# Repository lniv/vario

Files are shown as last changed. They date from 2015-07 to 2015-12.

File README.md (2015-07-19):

# vario

A sailplane / soaring  variometer project.
Minimal use is as a standalone vario, using a pressure sensor (typically connected to a TE probe) to measure climb rate. The code running on a teensy 3.1  (using the teensyduino environment (but not the IDE (shudder)) drives an indicator gauge stepper and a speaker.
Optionally, a differential pressure sensor and a gps are connected to the uC, and information is sent to a flight computer.
Current protocol implemented is the open vario one, and the gps GPRMC sentences are just echoed.
Currently a 9dof imu is connected as well, but the data is not procssed. In the far future one could integrate barometric / imu / gps data to get a better state estimate.

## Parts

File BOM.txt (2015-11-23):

BOM

The following components were used - initially on a protoboard, moved onto a soldered setup. This is not the cheapest or smallest way to use the underlying components, but the point was to use a building block approach and avoid any surface mount soldering, or creating PCBs (though assembling all of these using 30 awg wire, as i've done, does resemble a rats nest - i will try to create a pcb for easily connecting all of these)

Adafruit 

1 x Teensy 3.1 + header[ID:1625] = $19.95
1 x Adafruit 10-DOF IMU Breakout - L3GD20H + LSM303 + BMP180[ID:1604] = $29.95
1 x Adafruit Mono 2.5W Class D Audio Amplifier - PAM8302[ID:2130] = $3.95
1 x Mini Metal Speaker w/ Wires - 8 ohm 0.5W[ID:1890] = $3.00
1 x Automotive Gauge Stepper Motor (x27.168) [ID:2424] = $9.95
1 x Adafruit TB6612 1.2A DC/Stepper Motor Driver Breakout Board[ID:2448] = $4.95

modern device -  Pressure Sensor (MPXV) (#MD0590) (honeywell MPXV7007DP) 14$
2 x 10K resistors (for MPXV7007DP voltage divider) - should be 1% or better.

Sparkfun:
1 x LS20031 gps module [Sparkfun GPS-08975] = 59.95$

1 x MS-5611 breakout module GY-63 [dealextreme #148866, numerous sources exist] = 14.35$

Notes:
currently the code does not use the gps (apart from forwarding it to the navigation computer), the diff pressure module (ditto - it does calculate airspeed, but does not use it for vario) and imu. Hence, a simpler BMP180 breakout board can be used and the gps and diff pressure modules can be dropped, or only the MS-5611 breakout module can be used (dropping gps, imu)

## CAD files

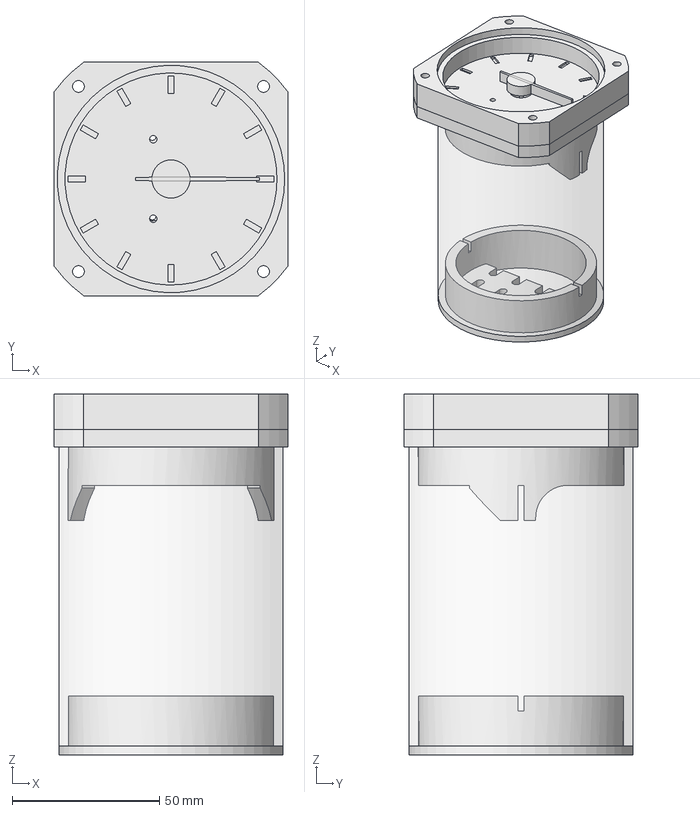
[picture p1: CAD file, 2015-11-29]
mechanical/v1/vario_assembly_v1.fcstd
79.4 x 79.4 x 122.6 mm
fron_window_holder_v1_01
vario_body_rev5_01
vario_rear_r2_01
stepper_gauge_x27168_01
dial_01
body_tube_v1_01

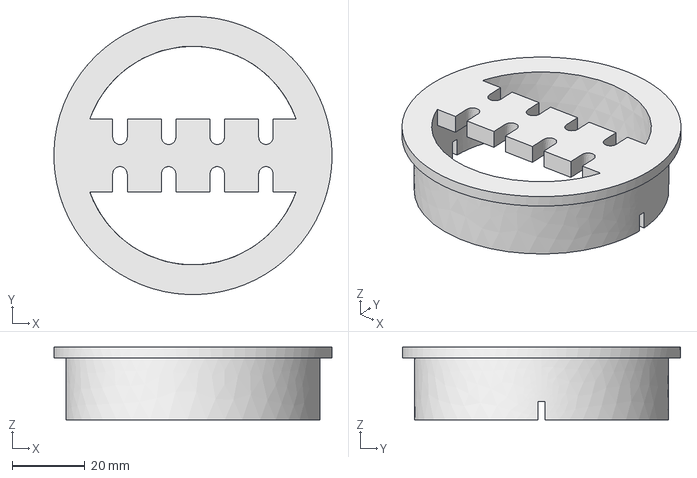
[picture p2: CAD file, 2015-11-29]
mechanical/v1/vario_rear_r2.fcstd
76.2 x 76.2 x 20.0 mm

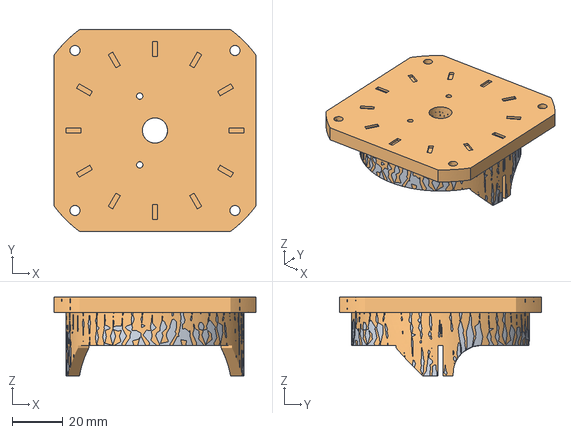
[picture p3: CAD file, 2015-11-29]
mechanical/v1/vario_body_rev5.fcstd
79.4 x 79.4 x 31.0 mm
Chamfer001 (Meshed)

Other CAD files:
mechanical/v1/vario_front_ring_rev5.fcstd
mechanical/v1/vario_body_rev5.stl
mechanical/v1/vario_front_ring_rev5.stl
mechanical/v1/vario_rear_r2.stl

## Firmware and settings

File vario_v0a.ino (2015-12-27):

// Simple presure based variometer, using a bmp180 / ma5611 to drive an audio and a stepper needle.
// also has a gps and a diff pressure measuring airspeed, but those are used for sending to a FC, not for vario functionality at prsent.
// Copyright Niv Levy July 11th 2015 and later
// released under GPL v2

// TODO : clean up, get rid of the buffer and unused bits of code e.g. the regression fit.
// TODO: separate the lowpass filters for driving the stepper / audio (which can be fast - 0.5sec or so - from the info sent to the computer, which must not have information above 0.5Hz (to be conservative, 0.8 * f_Nyquist = 0.4Hz for a 1Hz message rate)

// Using openvario protocol - follow https://github.com/Turbo87/openvario-protocol

// originally based on http://www.rcgroups.com/forums/showthread.php?t=1749208  ( Rolf R Bakke, Oct 2012), but zero remains.
//ms5611 code adapated from http://forum.arduino.cc/index.php?topic=103377.0

// Total Energy source - if defined, use a MS5611 module (GY-63) on i2c, address 76; if not, use a BMP180. for now i'm including both and letting the compiler deal with it - i am using the altitude calculation from the bmp, and i'm not short of resources.
#define TE_MS5611 1

#define MS5611_CSB_PIN 16 // CSB pin (address)
#define MS5611_ADDRESS 0x76 

#define USE_STEPPER 1
#define MAKE_NOISE 1

#include <Wire.h>
#include <Adafruit_Sensor.h>
#include <Adafruit_BMP085_U.h>
#include <Stepper.h>
#include <TimerOne.h>
#include <TinyGPS.h>
#include <ADC.h>

#define speaker_PIN 10

#define DPducer_PIN 14
ADC *adc = new ADC(); // adc object;


#ifdef USE_STEPPER
// change this to the number of steps on your motor
#define STEPS 100
// create an instance of the stepper class, specifying
// the number of steps of the motor and the pins it's
// attached to
// was 4,5,6,7 moving to 3,4,5,6 to free 7 and 8 for serial port
Stepper stepper(STEPS, 3, 4, 5, 6);
    
// how many steps per m/sec of climb rate (or something - units are still uncertain at this point in time. assuming we want a 20kt range (+-10kt) = 10m/sec range over 600 steps -> 1m/sec is 60 steps
// either i got something above wrong, but it seemed that 0.5m/sec move the needle 1/3 scale!
#define STEP_MULT 60.0 // 

#endif //USE_STEPPER

// i'm going to do the filtering not so nicely, by just implementing a ring buffer, storing deltas and going from there. Since bmp180 seems to get about 30Hz, and i'd like at most 0.5sec, we'll start with 20 samples.
// we should at least use a non square window, TODO
#define N_samples 75 // 25sampls/sec and a 1.5sec time constant : 37.5 samples x 2  = 75

const int dT = 40; // time between samples, msec

const float Fs = 1000.0F / dT; // sampling rate [Hz]

const float ddsAcc_limit = dT * 2;
const float sound_threshold = ddsAcc_limit / 2;

// audio dead band [m/sec]
const float neg_dead_band = -0.5F;
const float pos_dead_band = 0.5F;

float H[N_samples];
float sample_times[N_samples];
float delta_times[N_samples];
float lrCoef[2];

byte counter = 0;
bool grab_data = false;
long since_last;
// use the first N packets to estimate speed bias
#define N_bias_packets 1000
//could be moved to setup
int bias_packets = N_bias_packets; 
float speed_bias = 0.0f; // m/sec

elapsedMillis t = 0;

Adafruit_BMP085_Unified bmp = Adafruit_BMP085_Unified(BMP085_MODE_ULTRAHIGHRES);

// gps connected to Serial1
TinyGPS gps;
#define Uart Serial1

// FC connected on pins 7,8; pin8 is tx 
#define FC Serial3

void time_isr(void) {
    since_last = long(t);
    t = 0;
    grab_data = true;
}



unsigned long time = 0, last_time = 0;

float toneFreq, pressure, altitude, old_altitude;

float ddsAcc; // int is 4 bytes on the later arduino and teensy!

short position, old_position;

float dp_offset;

// keep track of gps message and just copy it when it's done. we don't actually need the parser, but i'll use it to see when a message is finished!
String gps_s = String();

#ifdef TE_MS5611

uint16_t ms5611_C[7]; // compensation coefficients for the ms5611

//initialize ms5611, read coefficients
void ms5611_initial() {

    Serial.println();
    Serial.println("ms5611 PROM COEFFICIENTS");

    Wire.beginTransmission(MS5611_ADDRESS);
    Wire.write(0x1E); // reset
    Wire.endTransmission();
    delay(10);


    for (int i=0; i<6  ; i++) {

        Wire.beginTransmission(MS5611_ADDRESS);
        Wire.write(0xA2 + (i * 2));
        Wire.endTransmission();

        Wire.beginTransmission(MS5611_ADDRESS);
        Wire.requestFrom(MS5611_ADDRESS, (uint8_t) 6);
        delay(1);
        if(Wire.available()) {
            ms5611_C[i+1] = Wire.read() << 8 | Wire.read();
        }
        else {
            Serial.println("ms5611 - Error reading PROM 1"); // error reading the PROM or communicating with the device
        }
        Serial.println(ms5611_C[i+1]);
    }
    Serial.println();
}

//get ms5611 value for a given code
long ms5611_getVal(byte code) {
    unsigned long ret = 0;
    Wire.beginTransmission(MS5611_ADDRESS);
    Wire.write(code);
    Wire.endTransmission();
    delay(10);
    // start read sequence
    Wire.beginTransmission(MS5611_ADDRESS);
    Wire.write((byte) 0x00);
    Wire.endTransmission();
    Wire.beginTransmission(MS5611_ADDRESS);
    Wire.requestFrom(MS5611_ADDRESS, (int)3);
    if (Wire.available() >= 3) {
        ret = Wire.read() * (unsigned long)65536 + Wire.read() * (unsigned long)256 + Wire.read();
    }
    else {
        ret = -1;
    }
    Wire.endTransmission();
    return ret;
}

//read ms5611 and return pressure in hPA
float ms5611_pressure() {
    uint32_t D1 = 0;
    uint32_t D2 = 0;
    int64_t dT = 0;
    int32_t TEMP = 0;
    int64_t OFF = 0;
    int64_t SENS = 0;
    int32_t P = 0;
    float Temperature;
    float Pressure;
    D1 = ms5611_getVal(0x48); // Pressure raw
    D2 = ms5611_getVal(0x58);// Temperature raw

    dT   = D2 - ((uint32_t)ms5611_C[5] << 8);
    OFF  = ((int64_t)ms5611_C[2] << 16) + ((dT * ms5611_C[4]) >> 7);
    SENS = ((int32_t)ms5611_C[1] << 15) + ((dT * ms5611_C[3]) >> 8);

    TEMP = (int64_t)dT * (int64_t)ms5611_C[6] / 8388608 + 2000;

    Temperature = (float)TEMP / 100;
    
    P  = ((int64_t)D1 * SENS / 2097152 - OFF) / 32768;

    Pressure = (float)P / 100;
    return Pressure;
}

#endif // TE_MS5611

// from b, a = signal.iirfilter(4, f0/f, btype = 'lowpass', ftype = 'butterworth')
double b[5] = {1.32937289e-05,   5.31749156e-05,   7.97623734e-05, 5.31749156e-05,   1.32937289e-05};
double a[5] = {1.        , -3.67172909,  5.06799839, -3.11596693,  0.71991033};

class filter {
	public:
		filter() {
		    for (int i=0; i < 5; i++) {
			x[i] = 0.0;
			y[i] = 0.0;
		    }
		}
	private:
		double x[5], y[5];
	public:
		double step(double new_val) 
		{
		    int i;
		    for (i=0; i< 4; i++) { 
			x[i] = x[i+1];
			y[i] = y[i+1];
		    }
		    x[4] = new_val;
		    y[4]  = 0.0;
		    for (i=0; i< 5 ; i++) {
			y[4] += b[i] * x[4-i];
                    }
		    for (i=1; i < 5; i++) {
			y[4] -= a[i] * y[4-i];
                    }
		    //y[4] = y[4] / a[0]; // not needed since a[0] =1.0;
			return y[4];
		}
};
    
filter Vz_lowpass, Vx_lowpass;

const float R =  8.31432; // N·m/(mol·K)
const float Tb = 288.15; //K
const float L_b = -0.0065;  // K/m
const float g = 9.80665; // m/s2
const float M =  0.0289644; // kg/mol
const float roe_0 = 1.225; // kg/m^3
const float Vcc = 5.0;//(NOTE: we could measure this using an a2d channel and a divider

// calculate true airspeed based on pressure and differential pressure.
// following densiy model to 11Km
float TAS(float altitude) {
    float EAS, volts, q, roe, TAS;
    int value;
    // from wikipedia 
    // TAS = EAS * sqrt(roe_0 / roe)
    // EAS = sqrt(2*q/ roe_0)
    //where ro_0 = see level density 1.225 kg/m^3, q is dynamic pressure
    
    // transfer function for a MPXV7007 is Vout = Vs *(0.057*P + 0.5) + error
    // we have a 2:1 voltage divider on the output to stay below 3.3V
    // slope is fixed within 1% and we can ignore it, offset we'll take at startup, for what that's worth - ot maybe calibrate once?
    
    //read diff pressure directly (nothing else needs it)
    //dp_offset : signal at P=0 -vs/4
    value = adc->analogRead(DPducer_PIN); // = Vout / 2 = Vs/2 * (0.057*P + 0.5) + error/2
    q = (((float) value)  / 65535.0f - 0.5) / 0.057; //kPa
    /*
    volts = value * 2.5 / adc->getMaxValue(ADC_0);
    //Serial.println(volts - dp_offset);
    // notes above are wrong now - the offset is part of the dp_offset recorded at start
    q = (volts - dp_offset) * 2.0/ (Vcc * 0.057); //kPa
    */
    //Serial.println(q);
    // TODO: i'm not sure what is a legit thing to do - i can think of cases where pitot is lower than static, but whether to treat them as real airspeed or just throw them out is unclear to me. (i.e. it's essentially something/one sucking on the pitot - but i can think of a transient during e.g. a tail slide that would do this)
    if (q>0) {
	EAS = sqrt(2*q * 1000.0 / roe_0); // m/sec
    }
    else {
	EAS = -sqrt(2*(-q) * 1000.0 / roe_0); //m/sec
    }
    //https://en.wikipedia.org/wiki/Barometric_formula
    
    roe = roe_0 * pow((1- L_b * altitude/Tb), 1 + g * M / (R -L_b));
    TAS = EAS * sqrt(roe_0/roe);
    return TAS;
}    


// send a single POV sentence
void send_POV(float x, char t) {
    byte checksum = 0;
    unsigned int i;
    int N, frac;
    float abs_x = abs(x);
    String ex_zero = String(), s = String(), ps = String();
    
    N = floor(abs_x);
    frac = floor((abs_x - N) * 100); // need two decimal places
    if (frac < 10)
	ex_zero += "0";

    if (x >=0) {
	ps = ps + "POV," + t + "," + N + "." + ex_zero + frac;
    }
    else {
	ps = ps + "POV," + t + ",-" + N + "." + ex_zero + frac;
    }
    // checksum calculation from https://rietman.wordpress.com/2008/09/25/how-to-calculate-the-nmea-checksum/
    for (i=0; i< ps.length(); i++) {
	checksum ^= ps[i]; 
    }
    s = s + "$" + ps + "*";
    Serial.print(s);
    Serial.println(checksum, HEX);
    FC.print(s);
    FC.println(checksum, HEX);
    return;
}

// send information to flight computer (tophat, xcsoar..) using openvario spec, as defined at
// https://github.com/Turbo87/openvario-protocol
//$POV,<type>,<value>,<type>,<value>,...*<checksum>
void info2FC(float airspeed, float climb_rate, float pressure) {
    send_POV(airspeed * 3.6, 'S'); // convert to km/h
    send_POV(climb_rate, 'E');  // already in m/sec
#ifndef TE_MS5611
    send_POV(pressure / 100.0, 'P');  //already in hPa (wtf? i guess it's actually in Pa)
#else
    send_POV(pressure, 'P');  //hPa
#endif TE_MS5611
    return;
}


void setup()
{
    int i, value;
    float volts;
    
    //setup the MS5611 for correct i2c address
    // put pin 16 output, pulled high - CSB on ms5611, select 76 or 77
    pinMode(MS5611_CSB_PIN, OUTPUT);
    digitalWrite(MS5611_CSB_PIN, HIGH);
    
#ifdef TE_MS5611 // no idea if this is really needed, handled somewhere else etc
    // Disable internal pullups, 10Kohms are on the breakout
    PORTC |= (1 << 4);
    PORTC |= (1 << 5);
#endif // TE_MS5611
    
    //handle the adc measuring the diff pressure (airspeed sensor)
    pinMode(DPducer_PIN, INPUT);
    adc->setReference(ADC_REF_EXT, ADC_0); // might make sense to use the more stable 1.2V, but need to change scaling
    adc->setAveraging(64); // set number of averages
    adc->setResolution(14); // set bits of resolution
    adc->setConversionSpeed(ADC_HIGH_SPEED_16BITS); // change the conversion speed
    adc->setSamplingSpeed(ADC_HIGH_SPEED_16BITS); // change the sampling speed
    
    /* Initialise the sensor */
    if(!bmp.begin())
    {
	/* There was a problem detecting the BMP085 ... check your connections */
	Serial.print("Ooops, no BMP180 detected ... Check your wiring or I2C ADDR!");
	while(1);
    }
    Serial.begin(115200); // note that number i BS for teensy.
    delay(2000); // debug only, for seeing serial start on arduino console.  FIXME - comment out. 
    // just a place to start - should be actual pressure, but whatever
    //initialize pressure
    bmp.getPressure(&pressure);
    old_altitude = bmp.pressureToAltitude(SENSORS_PRESSURE_SEALEVELHPA, pressure / 100.0F);
    
    for (i =0; i < N_samples; i++) {
	H[i] = old_altitude;
	sample_times[i] = 0.0;
    }
    /*
    //calculate diff pressure offset:
    dp_offset = 0.0;
    //dp_offset : signal at P=0 -vs/4
    // Vs = 5.0 (NOTE: we could measure this using an a2d channel and a divider
    for (i=0; i< 200 ;i++) {
	value = adc->analogRead(DPducer_PIN);
	volts = value * 3.3 / adc->getMaxValue(ADC_0);
        Serial.println(volts);
	dp_offset += volts;// - Vcc / 4.0;
    }
    dp_offset = dp_offset / 200.0;
    */
#ifdef USE_STEPPER
    stepper.setSpeed(300);
    // try to get it to center
    // uncomment this if necessary to set - but it does bang the motor against the stop!
    stepper.step(-600);
    stepper.step(300);
    old_position = position = 300;
#endif //USE_STEPPER

#ifdef TE_MS5611
    ms5611_initial();
#endif //TE_MS5611
    
    Timer1.initialize(dT * 1000);
    Timer1.attachInterrupt(time_isr);
    
    Uart.begin(57600);
    
    FC.begin(4800);
    
    Serial.println("start");
    Serial.print("dp offset = ");
    Serial.print(dp_offset);
    Serial.println("V");
}

int gps_messages = 0;
String last_gps = String();

void loop()
{
    int i;
    long since_last_copy;
    float climb_rate, climb_rate_filter, airspeed;
    

    if (Uart.available()) {
	char c = Uart.read();
 	 //   Serial.print(c);  // uncomment to see raw GPS data
	if (c == '$') {
	    gps_s = String() + '$';
        }
	else {
	    gps_s = gps_s + c;
        }
	if (gps.encode(c)) {
	    long lat, lon;
	    unsigned long age;
	    gps.get_position(&lat, &lon, &age);
	    //Serial.print("Lat/Long(10^-5 deg): "); Serial.print(lat); Serial.print(", "); Serial.print(lon); 
	    //Serial.print(" Fix age: "); Serial.print(age); Serial.println("ms.");
	    /*
	    if (gps_s.startsWith("$GPGGA")) {		  
		    Serial.println(gps_s);
	    }*/
	    //Serial.println(gps_s);
	    if (gps_s.startsWith("$GPRMC")) {
// 	    if (gps_s.startsWith("$GPGGA"))
		last_gps = gps_s;
            }
	    gps_s = String();
	}
    }
    if (grab_data) {
	
	noInterrupts();
	since_last_copy = since_last;
	grab_data = false;
	interrupts();
	
#ifndef TE_MS5611
	bmp.getPressure(&pressure);
        pressure /= 100.0F;
#else
        pressure = ms5611_pressure();
#endif // TE_MS5611
        //Serial.println(bmp.pressureToAltitude(SENSORS_PRESSURE_SEALEVELHPA, pressure));
	H[counter % N_samples] = bmp.pressureToAltitude(SENSORS_PRESSURE_SEALEVELHPA, pressure);

	sample_times[counter % N_samples] = float(millis());
	for (i=0; i<N_samples ; i++) {
	    delta_times[i] = sample_times[i] - sample_times[0];
        }
	
	// NOTE : the filter here is for a fixed 25Hz sampling rate!
	if (counter > 0) {
	    climb_rate_filter =  Vz_lowpass.step(Fs * (H[counter % N_samples] - H[(counter-1) % N_samples]));
        }
	else  {// KLUDGE
	    climb_rate_filter =  Vz_lowpass.step(Fs * (H[0] - H[N_samples-1]));
        }
	airspeed = Vx_lowpass.step(TAS(H[counter % N_samples]));
	if (bias_packets) { 
            bias_packets--;
            speed_bias += airspeed / N_bias_packets;
            if (bias_packets % 10 == 0 && bias_packets) {
                Serial.print("speed bias = ");
                Serial.print(speed_bias);
                Serial.print(" N_packets = ");
                Serial.println(bias_packets);
            }
            else if (bias_packets == 0) {
                Serial.print("final speed bias = ");
                Serial.println(speed_bias);
            }
        }
	//climb_rate = lrCoef[0] * 1000; // in m/sec
	climb_rate = climb_rate_filter;

#ifdef USE_STEPPER
	old_position = position;
	position = constrain(300 - int(climb_rate * STEP_MULT), 0, 600);
	stepper.step(position - old_position);
#endif //USE_STEPPER
        
	// NOTE: can do non linear function here, e.g. logarithmic
	// scaled so 5/msec is full range
	toneFreq = constrain(climb_rate * 100, -500, 500);
	
	// copied from my mkiv audio code
	if (toneFreq > 0) {
	    toneFreq += 150 ; 
        }
	ddsAcc += climb_rate * 100.0;
	if (ddsAcc > ddsAcc_limit) {
	    ddsAcc = 0;
        }
	if (ddsAcc < 0) {
	    ddsAcc = 0;
        }
/*
	Serial.print("i= ");
	Serial.print(counter);
	Serial.print(", dt (ms)= ");
	Serial.print(since_last_copy);
    //     Serial.print(", P= ");
    //     Serial.print(pressure);
	Serial.print(", Alt= ");
	Serial.print(H[counter % N_samples]);
	Serial.print("m , lrCoef: ");
	Serial.print(lrCoef[0] * 1000);
	Serial.print(" m/sec,");
	Serial.print(lrCoef[1]);
	Serial.print(" m, f= ");
	Serial.print(toneFreq + 510);
	Serial.print(", ddsAcc = ");
	Serial.print(ddsAcc);
	Serial.print(", climb_rate_filter = ");
	Serial.print(climb_rate_filter);
	Serial.print(", positions = ");
	Serial.print(position);
	Serial.print(",");
	Serial.print(old_position);
	//value = adc->analogRead(DPducer_PIN);
	//Serial.print(", DP= ");
	//Serial.println(value*3.3/adc->getMaxValue(ADC_0), DEC);
	Serial.print(", V= ");
	Serial.print(airspeed);
	Serial.println(" m/sec");
*/

#ifdef MAKE_NOISE
	// using the linear regression instead of my stupidity
	//if (climb_rate < neg_dead_band || ( climb_rate > pos_dead_band && ddsAcc > sound_threshold))
	if (climb_rate < neg_dead_band || ( climb_rate > pos_dead_band && counter % 12 > 6)) {
	    tone(speaker_PIN, toneFreq + 510);
        }
	else {
	    noTone(speaker_PIN);
        }
#endif // MAKE_NOISE
	// send info every 1sec
	if (counter % 25 == 0) {
	    info2FC(airspeed - speed_bias, climb_rate_filter, pressure);
	    Serial.println(last_gps.trim());
	    FC.println(last_gps.trim());
	}
	counter++;
    }
}

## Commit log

2015-07-13 Replaced linear regression of heights with a (sort of) proper iir bessel filter that i got from filtduino. Does seem to behave somewhat better.
    [vario_v0a.ino]
2015-07-13 Replaced the variable chopping with a fixed one (could never get it to sound nice) back to a single pole iir filter, seems stable stepper is now consistent and matches climb rate. it might be worthwh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
    [vario_v0a.ino]
2015-07-13 Added a BOM
2015-07-18 minimal adc code to read a diff pressure sensor (MXPV7007DP) connected to the teensy (not doing anything with it beyond logging to serial)
2015-07-18 added airspeed calculation. filtered the same as the vario. despite trying to get a sensor offset at start, seems to gather an offset later and stabilize at a few m/sec offset.
    [vario_v0a.ino]
2015-07-19 Calculate airspeed and send airspeed, pressure and vario to FC using openvario protocol - which i'm not sure if working (or maybe somehting else is wrong). In any case, i can connect to the nook and 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
    [vario_v0a.ino]
2015-07-19 Added a pseudo schematic - done in inkscape in a lego block style, to match overall project.
2015-11-23 Added a MS-5611 module and code to drive it (and corrected schematics, BOM to match). A define statment chooses between using it and the BMP180 as the pressure sources. Also corrected a scaling for v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
    [vario_v0a.ino]
2015-11-29 adding a first revision of mechanicals; i have printed the three files attached and assembled (using a 3" od. x 1/8" wall acrylic tube as the body) However, the rear piece is more of a place holder -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
    [vario_body_rev5.fcstd, vario_body_rev5.stl, vario_front_ring_rev5.fcstd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]
2015-11-29 adding assembly
    [vario_assembly_v1.fcstd]
2015-11-30 fixed an extra carriage return which was breaking communication with recent TopHat / xcsoar - at some point the generic nema parsing became stricter.
    [vario_v0a.ino]
2015-12-27 airspeed: changed TAS calculation, using a the first N readings to establish a baseline - currently starting in flight would be bad. changed ADC to use a 1:1 splitter on the 5V supply as the referenc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
    [vario_v0a.ino]
